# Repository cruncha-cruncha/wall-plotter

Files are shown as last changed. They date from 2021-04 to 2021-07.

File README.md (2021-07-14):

# Wall Plotter

The all-in-one wall plotting solution. Do you like walls? Do you like line drawings? Do you wish you could draw stuff without all the hassle of lifting your pen up? Then you need the wall plotter.  

This project is a 2d plotter. Consists of a brain box (arduino), two stepper motors, some 3D prints, and fishing line, that's it. Basic conceptual physical setup: Two spools of fishing line are placed 100cm apart horizontally, their ends are tied together around a pen. By rotating the spools, the pen will draw on the wall.  

Actually used:
- two Nema 17 motors (17HS4401)
- wood 2-4 for mounting
- some screws for mounting
- GRBL arduino shield [here](https://blog.protoneer.co.nz/arduino-cnc-shield/)
- 24V 2A DC power cable with screw terminal adapter for the shield/motors
- Arduino Uno
- a very long A-to-B usb cable
- 3D printed parts
- elastic bands
- sharpie markers
- 40lb braided fishing line
- 18 gauge copper wire
  - guide the fishing line
  - smoothly attach the pen holder to the fishing line
  - attach power cable to the GRBL board

Aside from the physical setup, there are three (3) important software steps:
1. [Generate motor control pulses (via a handy website)](https://cruncha-cruncha.github.io/wall-plotter/)
2. [Send pulses to Arduino (via a python script)](https://github.com/cruncha-cruncha/wall-plotter/blob/main/other/send.py)
3. [Receive pulses on Arduino (via some C code)](https://github.com/cruncha-cruncha/wall-plotter/blob/main/other/receive/receive.ino)

## Limitations
Step #1 (the website that generates motor control pulses) only accepts svg files. In those files, only paths will be processed. Also, any transform styling will be ignored.

## Algorithm
For each path in the svg:
1. sample a point every Xmm along the path
2. remove points based on a smoothing algorithm
3. calculate the top speed between every two points based on the distance between them
4. traverse straight between each pair of points

In reality, 1, 2, and 3 happen in the same loop for efficiency. See [this file](https://github.com/cruncha-cruncha/wall-plotter/blob/main/src/components/Converter/useConverter.js) for the code.

### Notes

1. Xmm is 2mm by default
2. Smoothing algorithm works as follows:
  1. Set `precision` to 2mm
  2. For each set of points a, b and candidate point c, where a.length < b.length < c.length along the path:
  3. Calculate the shortest distance D from point b to a line passing through points a and c
  4. If D is less than `precision`, discard point b and replace with point c, set `precision` to `precision` / 2
  5. If D is greater than `precision`, keep all points, use a = b and b = c in the next loop
  The result of this algorithm is that:
  - points residing inside straight lines are discarded
  - small aberrations (less than 2mm deviation from neighbouring points) are discarded
  - sharp corners are preserved
  - gradual but persistent changes (low frequency oscillations) are preserved
  - less points are carried over to step #4
3. Top speed is a number from 0 to 7 inclusive, interpreted linearly by the Arduino, and based on a simple lookup. See `getSpeed()`. Speed is per-motor-pulse, and is converted into a wait time between pulses. Step four ramps linearly from current speed, to top speed. If the next line has a lower top speed, it then ramps down to that speed.
4. Given a current known location/fishing-line-length, figure out exact fishing-line-length for the desired location (next point). Linearly intersperse motor pulses to get as close to that fishing-line-length as possible. This may trace a slightly curved line on the wall. Figure out new cartesian coordinate given actual fishing-line-length. Repeat.

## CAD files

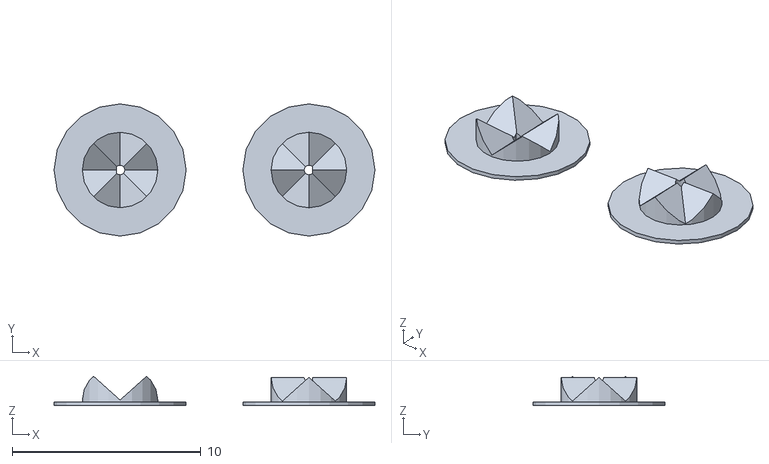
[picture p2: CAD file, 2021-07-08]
stls/2-part Spool.stl
17.0 x 7.00 x 1.55

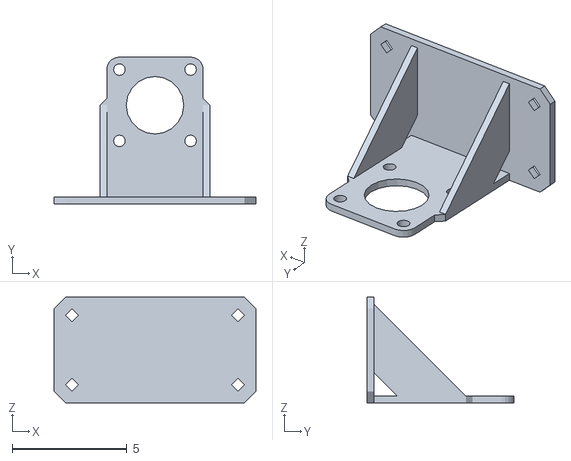
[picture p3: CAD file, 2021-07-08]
stls/Nema 17 Mount.stl
8.80 x 6.40 x 4.60

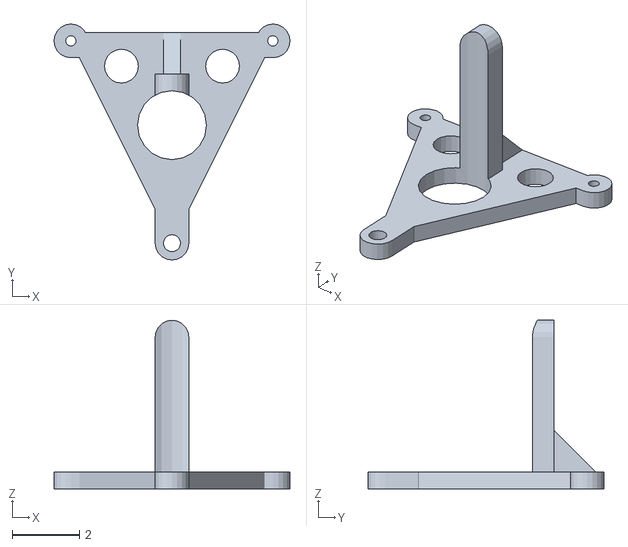
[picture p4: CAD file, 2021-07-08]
stls/Better Tool Holder.stl
7.00 x 7.00 x 5.00

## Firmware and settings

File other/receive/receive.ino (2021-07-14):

#define enablePin 8

// X (left)
#define xDirPin 5
#define xStepPin 2

// Y (right)
#define yDirPin 6
#define yStepPin 3

byte buf[1];

void setup() {
  Serial.begin(9600);
  Serial.setTimeout(1);
  while (!Serial) {
   delay(1);
  }

  pinMode(enablePin, OUTPUT);
  pinMode(xStepPin, OUTPUT);
  pinMode(xDirPin, OUTPUT);
  pinMode(yStepPin, OUTPUT);
  pinMode(yDirPin, OUTPUT);

  digitalWrite(xStepPin, LOW);
  digitalWrite(yStepPin, LOW);
}

void leftShorter() {
  digitalWrite(xDirPin, HIGH);
  digitalWrite(xStepPin, HIGH);
}

void leftLonger() {
  digitalWrite(xDirPin, LOW);
  digitalWrite(xStepPin, HIGH);
}

void leftHold() {
  digitalWrite(xStepPin, LOW);
}

void rightShorter() {
  digitalWrite(yDirPin, HIGH);
  digitalWrite(yStepPin, HIGH);
}

void rightLonger() {
  digitalWrite(yDirPin, LOW);
  digitalWrite(yStepPin, HIGH);
}

void rightHold() {
  digitalWrite(yStepPin, LOW);
}

void loop() {
  if (Serial.available() > 0) {

    Serial.readBytes(buf, 1);

    if (buf[0] == 0xff) {
      // enable
      digitalWrite(enablePin, LOW);
      delay(1);
      return;
    } else if (buf[0] == 0x88) {
      // disable
      digitalWrite(enablePin, HIGH);
      delay(1);
      return;
    }

    byte motorDirs = buf[0] & 0x07;
    if (motorDirs == 0x00) {
      leftHold();
      rightLonger();
    } else if (motorDirs == 0x01) {
      leftHold();
      rightShorter();
    } else if (motorDirs == 0x02) {
      leftLonger();
      rightHold();
    } else if (motorDirs == 0x03) {
      leftLonger();
      rightLonger();
    } else if (motorDirs == 0x04) {
      leftLonger();
      rightShorter();
    } else if (motorDirs == 0x05) {
      leftShorter();
      rightHold();
    } else if (motorDirs == 0x06) {
      leftShorter();
      rightLonger();
    } else if (motorDirs == 0x07) {
      leftShorter();
      rightShorter();
    }

    byte speed = (buf[0] & 0x38) >> 3;
    unsigned long pauseMS = 2995 - (speed * 285);

    delayMicroseconds(pauseMS);
    
    digitalWrite(xStepPin, LOW);
    digitalWrite(yStepPin, LOW);
    
    delayMicroseconds(pauseMS);

    Serial.write(buf, 1);
    
  } else {
    delay(5);
  }
}

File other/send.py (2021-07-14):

import keyboard
import serial
import time
import json
import os

PORT = 'COM3'
BAUDRATE = 9600

COMMANDS = {
    "enable":  b'\xff',
    "disable": b'\x88'
}

def stepToHex(step):
    if (not 's' in step) or (not 'l' in step) or (not 'r' in step):
        # error
        return COMMANDS["disable"]
    if step['l'] == 0 and step['r'] == 0:
        # aka no-op
        return COMMANDS["enable"]
    
    # 1  = longer
    # 0  = hold
    # -1 = shorter
    motorDirections = None
    if step['l'] == 0 and step['r'] == 1:
        motorDirections = b'\x00'
    elif step['l'] == 0 and step['r'] == -1:
        motorDirections = b'\x01'
    elif step['l'] == 1 and step['r'] == 0:
        motorDirections = b'\x02'
    elif step['l'] == 1 and step['r'] == 1:
        motorDirections = b'\x03'
    elif step['l'] == 1 and step['r'] == -1:
        motorDirections = b'\x04'
    elif step['l'] == -1 and step['r'] == 0:
        motorDirections = b'\x05'
    elif step['l'] == -1 and step['r'] == 1:
        motorDirections = b'\x06'
    elif step['l'] == -1 and step['r'] == -1:
        motorDirections = b'\x07'

    speed = step['s'] << 3

    return bytes([motorDirections[0]|speed])

class Plotter:
    def __init__(self, port, baudrate):
        self.port = port
        self.baudrate = baudrate
        self.connect()

    def connect(self):
        try:
            self.arduino = serial.Serial(port=self.port, baudrate=self.baudrate, timeout=0.1)
            print(" 2 second pause to allow Arduino to connect...", end='', flush=True)
            time.sleep(2)
            print(" done")
        except:
            print(" Failed to connect to arduino")

    def send(self, cmd):
        try:
            self.arduino.write(cmd)
        except:
            print("failed to send")

    def receive(self, length):
        try:
            return self.arduino.read(length)
        except:
            print("failed to receive")
            return []

class Standby:
    def go(self, controller):
        controller.send(COMMANDS["enable"])

        print()
        print(" Standby mode")
        print(" q = quit")
        print(" m = manual mode")
        print(" l = load file")
        print(" r = run file")
        print()

        while True:
            key = input().strip()
            if key == "q":
                controller.send(COMMANDS["disable"])
                print("Goodbye")
                quit()
            elif key == "m":
                controller.setState(STATE["MANUAL"])
                return
            elif key == "l":
                controller.setState(STATE["LOAD"])
                return
            elif key == "r":
                controller.setState(STATE["RUN"])
                return
            time.sleep(0.1)

class Load:
    def go(self, controller):
        print()

        if controller.input_file_path:
            print(" Currently: {}".format(controller.input_file_path))
        else:
            print(" Currently: no file")

        file_path = input(" Please enter file path: ").strip()

        if (not os.path.exists(file_path)) or (not os.path.isfile(file_path)):
            print(" Bad path")
        else:
            print(" Good path")
            controller.input_file_path = file_path

        print(" returning to standby")
        print()
        controller.setState(STATE["STANDBY"])
        return

class Run:
    def __init__(self):
        self.chunk_size = 16

    def sendAll(self, controller, data):
        steps = map(lambda d: stepToHex(d), data)
        for cmd in steps:
            controller.send(cmd)

    def receiveSome(self, controller, length):
        total_recv = 0
        while total_recv < length:
            recv = controller.receive(length - total_recv)
            if len(recv) == 0:
                break
            else:
                total_recv += len(recv)
        return total_recv

    def go(self, controller):
        if not controller.input_file_path:
            print(" No file to run")
            controller.setState(STATE["STANDBY"])
            return

        print()
        print(" Run mode")
        print()
        time.sleep(0.1)
        
        with open(controller.input_file_path, 'r') as f:
            data = json.load(f)

            moves = data["pulses"]

            spare = len(moves) % self.chunk_size

            if not (spare == 0):
                self.sendAll(controller, moves[0 : spare])
                received = self.receiveSome(controller, spare)
                if not (received == spare):
                    print("ERROR: sent {} steps, received {}".format( spare, received))
                    controller.setState(STATE["STANDBY"])
                    return 

            if len(moves) > spare:
                self.sendAll(controller, moves[spare : spare + self.chunk_size])

                for i in range(1, (len(moves) - spare) // self.chunk_size):
                    self.sendAll(controller, moves[spare + (i * self.chunk_size) : spare + ((i+1) * self.chunk_size)])
                    received = self.receiveSome(controller, self.chunk_size)
                    if not (received == self.chunk_size):
                        print("ERROR: at chunk {}, sent {} steps, received {}".format(i, self.chunk_size, received))
                        controller.setState(STATE["STANDBY"])
                        return

                received = self.receiveSome(controller, self.chunk_size)
                if not (received == self.chunk_size):
                    print("ERROR: at last chunk, sent {} steps, received {}".format(self.chunk_size, received))
                    controller.setState(STATE["STANDBY"])
                    return

        print("Success")
        controller.setState(STATE["STANDBY"])
        return

class Manual:
    def go(self, controller):

        print()
        print(" Manual mode")
        print(" k = right longer")
        print(" j = right shorter")
        print(" f = left longer")
        print(" d = left shorter")
        print(" q = back to standby")
        print()

        default_speed = 3
        while True:
            if keyboard.is_pressed("k"):
                controller.send(stepToHex({ "s": default_speed, "l": 0, "r": 1 }))
            elif keyboard.is_pressed("j"):
                controller.send(stepToHex({ "s": default_speed, "l": 0, "r": -1 }))
            elif keyboard.is_pressed("f"):
                controller.send(stepToHex({ "s": default_speed, "l": 1, "r": 0 }))
            elif keyboard.is_pressed("d"):
                controller.send(stepToHex({ "s": default_speed, "l": -1, "r": 0 }))
            elif keyboard.is_pressed("q"):
                input()
                controller.setState(STATE["STANDBY"])  
                return
            time.sleep(0.001)
        
STATE = {
    "STANDBY": Standby(),
    "LOAD":    Load(),
    "RUN":     Run(),
    "MANUAL":  Manual(),
}
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

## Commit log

2021-04-03 Current assumptions won't work, need to do a big refactor. See note in useConverter.js
2021-04-05 Calculate motor pulses, switch coorsReady <-> specsReady, use spool radius instead of spool diameter
2021-04-13 Add python and arduino code to test motor control
2021-04-13 Can parse and send motor control
    [motorControl.json]
2021-04-13 Change pulse notation: use longer and shorter instead of clockwise and counterclockwise
    [send.py]
2021-04-13 Fix motorControl bug: not taking into account the tool offsets
2021-04-29 Calc steps per second and save to json, update verbiage
    [motorControl.json]
2021-07-03 Enable arduino motor control by defaul, disable on quit. Hide download link if plotter computation in progress
2021-07-08 Add stl files
    [2-part Spool.stl, Better Tool Holder.stl, Nema 17 Mount.stl]
2021-07-09 New command protocol between python script and arduino code
2021-07-09 Fix bad python byte parsing, and speeds going the wrong direction on the arduino, cleanup svg files
    [receive.ino, send.py]
